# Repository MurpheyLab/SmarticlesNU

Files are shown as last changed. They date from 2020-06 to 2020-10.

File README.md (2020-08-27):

# SmarticlesNU

This repository includes all the hardware design and software files for the smarticle system. Examples can be found in Code/Python/Examples. See [Smarticle Tracking](https://github.com/murpheylab/SmarticleTracking) for the a python AprilTag tracking library and [SmarticleSimulation](https://github.com/asamland/SmarticleSimulation) for a PyBullet simulator of the system.  

All documentation for the python modules in this repository is available [here](https://murpheylab.github.io/SmarticlesNU/)

Installing Python Dependencies
------------

You can install pyserial and the XBee Python library using pip

    $ pip install pyserial
    $ pip install digi-xbee

Running Your First Program
-----------
Use the included `SmarticleSyncGait.py` to test your setup. You will have to modify `PORT_NAME` to match the USB port name of the local XBee connected to your computer.  

Run the the following command to execute the code and keep the python script open  
    
    $ python3 -i SmarticleSyncGait.py
    
Then you can run this command to run the smarticles for 1 minute  

    >>> timed_sync(1)

Interfacing with The Xbees
---
To Change the settings of the Base Xbee, use [DIGI XCTU](https://www.digi.com/resources/documentation/digidocs/90001526/tasks/t_download_and_install_xctu.htm)  
The Settings for the base Xbee are the default settings for 802.15.4 firmware with these changes:  
<br>
        **1.** Change mode (AP) to API Enabled  
        **2.** Change Pan ID (ID) to 1984  
        **3.** Ensure address (MY) is 0  
        **4.** Change Destination Low Address (DL) to 0xFFFF (broadcast)  
        
You can also modify these settings in a simple serial console by entering command mode. See this [guide](https://cdn.sparkfun.com/learn/materials/29/22AT%20Commands.pdf) for more information.
    
Modifying Code on The Smarticles
---
To modify the code on the smarticles themselves, you will also need to instal MiniCore into the Arduino IDE and an SI Labs driver for the CP2104 chip.  
  <br> 
    Get the CP210x Driver for your OS: [SI Labs Drivers Link](https://www.silabs.com/products/interface/usb-bridges/classic-usb-bridges/device.cp2104?q=cp2104;page=1;x6=searchHeader;q6=Software)  
    Download Arduino IDE: [Arduino IDE Link](https://www.arduino.cc/en/Main/Software)  
    Follow the instructions to install in Arduino IDE: [MiniCore Link](https://github.com/MCUdude/MiniCore#how-to-install) 
    <br>
    
After Installing all these dependencies you will have to move the files from the Code/Arduino folder into your local Arduino folder (usually found in documents)  
<br>
        **1.**  Move the programmable_smarticle folder into your Arduino directory (should be then documents/Arduino/programmable_smarticle)  
        **2.**  Move the contents of the repo Arduino/libraries folder into your local Arduino/libraries folder  
    
You will have to restart the Arduino IDE and then you should be able to open the programmable_smarticle.ino sketch and you should see PWMServo, NeoHWSerial, and Smarticle in the Sketch->Include Library file menu.

To upload the program to the smarticle, use the follow board configuration under the tools file menu:  

  | Field | Value|
|:------------:|:-------------------------------:| 
| Board        | ATmega328                      | 
| Clock        | 8MHz External                   |  
| BOD          | BOD 2.7V                        |  
| Compiler LTO | LTO Enabled                     |  
| Variant      | 328PB                           |  
| Bootloader   | Yes (UART0)                     |  
| Port         | select USB port of SI Labs Chip |

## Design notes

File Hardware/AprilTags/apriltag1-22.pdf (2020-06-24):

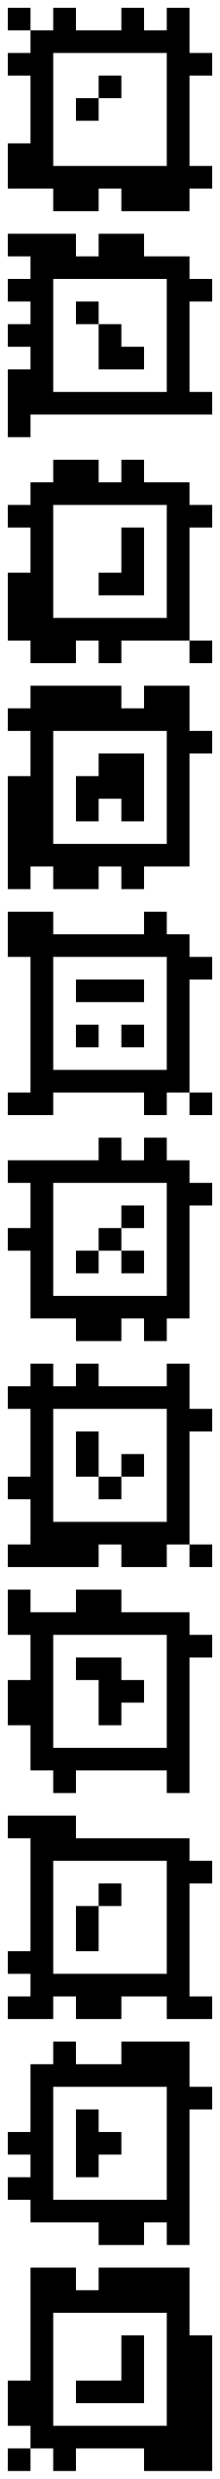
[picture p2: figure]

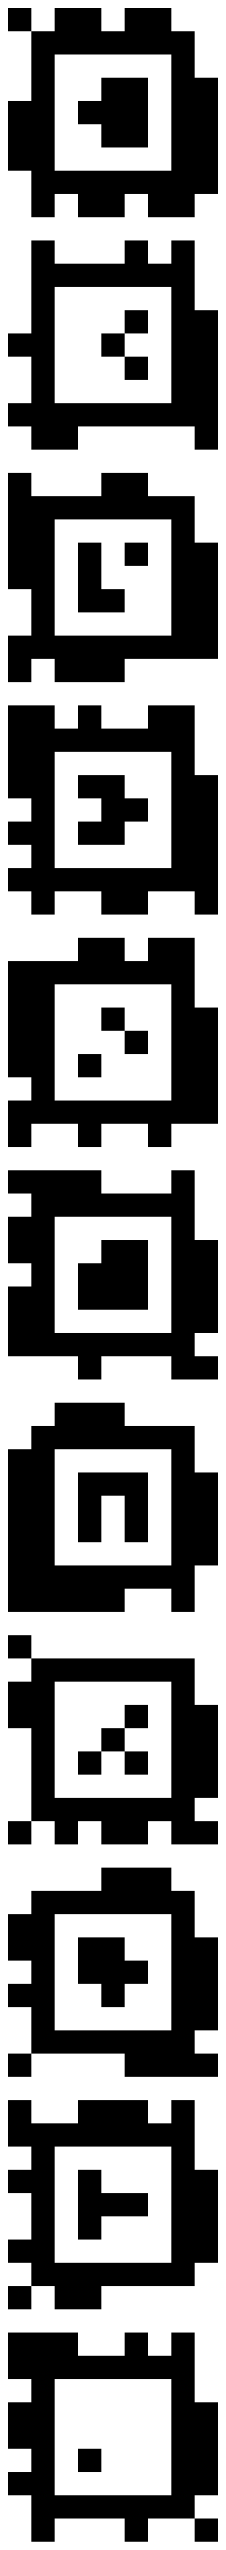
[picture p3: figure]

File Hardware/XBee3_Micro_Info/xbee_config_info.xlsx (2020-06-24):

node ID | device address (MY) | Serial No. | PAN ID | Coordinator Enable (CE) | API Mode (AP) | Destination Low Address (DL) | Serial No.
BASE | 0 | 41958C3B | 1984 | 1 | API w/esacpes (2) | FFFF (default is broadcast) | 41958C3B
smart1 | 1 | 41958CDB | 1984 | 0 | Transparent (0) | 0 | 41958CDB
smart2 | 2 | 41958C75 | 1984 | 0 | Transparent (0) | 0 | 41958C75
smart3 | 3 | 4195884A | 1984 | 0 | Transparent (0) | 0 | 4195884A
smart4 | 4 | 41958C55 | 1984 | 0 | Transparent (0) | 0 | 41958C55
smart5 | 5 | 4195890F | 1984 | 0 | Transparent (0) | 0 | 4195890F
smart6 | 6 | 41958C37 | 1984 | 0 | Transparent (0) | 0 | 41958C37
smart7 | 7 | 41958C7F | 1984 | 0 | Transparent (0) | 0 | 41958C7F
 | Serial number circled below

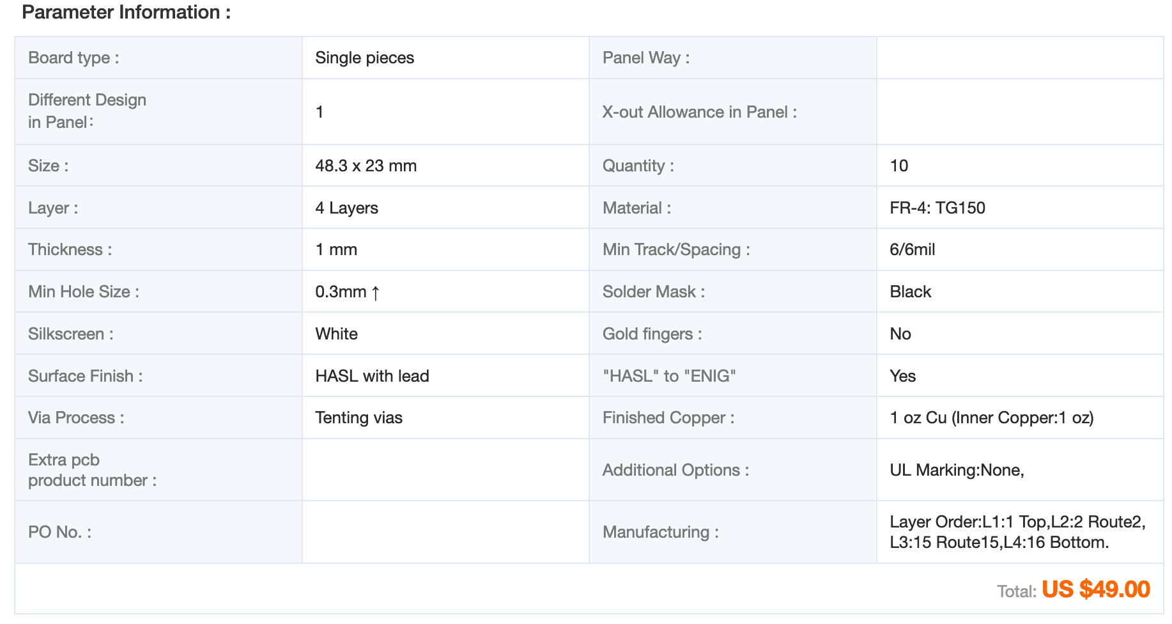
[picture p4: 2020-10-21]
Hardware/PCB/Eagle Files/PCBWay Parameters/Feather_PCBWay_params.png

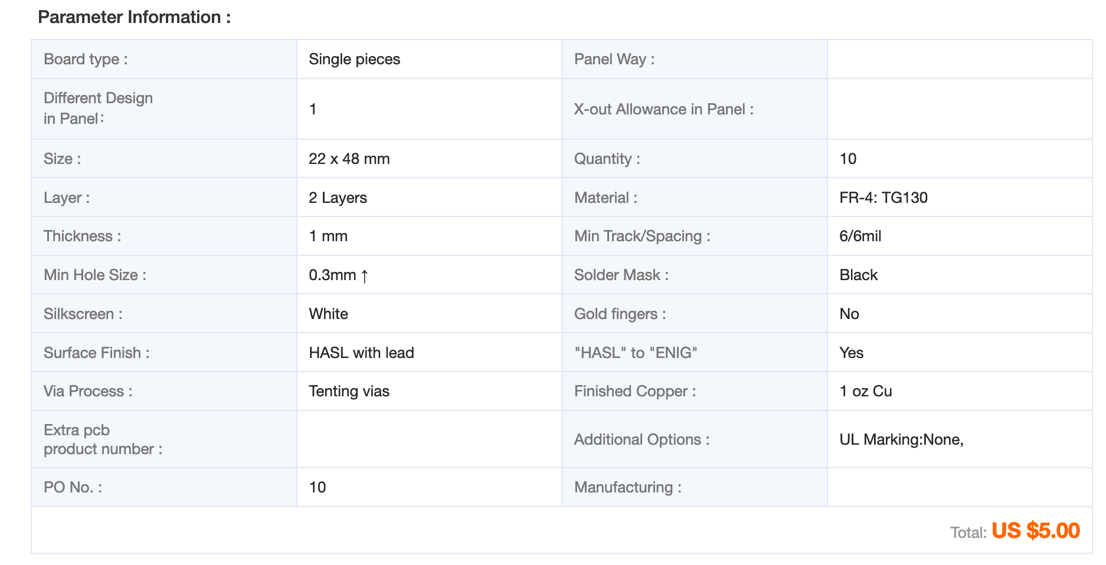
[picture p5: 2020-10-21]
Hardware/PCB/Eagle Files/PCBWay Parameters/TopBoard_PCBWay_params.png

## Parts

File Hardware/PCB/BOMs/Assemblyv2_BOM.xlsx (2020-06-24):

Item | Qty | Manufacturer | Mfg. Part No | Description
1 | 2 | Turnigy | 1440-A Servo (https://hobbyking.com/en_us/turnigytm-tgy-1440a-analog-servo-v2-0-8kg-0-10sec-4-4g.html) | Servos
2 | 1 | Molex | 51281-1294 (https://www.mouser.com/ProductDetail/Molex/51281-1294) | Connector b/w feather and top board
3 | 1 | eBoot | 1.25 mm JST 2 Pin Micro Female Connector (https://www.amazon.com/eBoot-Pairs-Electrical-Female-Connector/dp/B06WGM9W7S) | Battery connector
4 | 1 | Turnigy | nano-tech 200mAh 1S 35 (https://hobbyking.com/en_us/turnigy-nano-tech-200mah-1s-35-70c-lipoly-battery-5pcs.html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) | Battery

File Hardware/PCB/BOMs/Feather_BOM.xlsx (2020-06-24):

Item# | Ref Des | Qty | Manufacturer | Mfg Part no. | Package | Description/ Value | Type
1 | C8, C9, C11 | 3 |  |  | 0603 | 10nF | SMD
2 | C4, C6, C7, C10, C13 | 5 |  |  | 0603 | 0.1 uF | SMD
3 | C1,C14 | 2 |  |  | 0603 | 1.0uF | SMD
4 | C2,C3,C5,C12,C15 | 5 |  |  | 0603 | 10uF | SMD
5 | CON1 | 1 | Amphenol ICC | 10103594-0001LF |  | Micro B USB Connectors | SMD
6 | CON100 | 1 | Molex | 512811294 |  |  | SMD
7 | D1 | 1 |  |  | CHIP-LED 0603 | Red LED | SMD
8 | D2 | 1 | Diodes Inc. | SDM100K30L-7 | SOD-323 | Schottky Diode | SMD
9 | D3 | 1 |  |  | CHIP-LED 0603 | Orange LED | SMD
10 | Q1 | 1 | Didoes Inc. | DMG3418L | SOT23-R | P-Channel Mosfet | SMD
11 | R1, R2, R4, R6 | 4 |  |  | 0603 | 1K | SMD
12 | R3, R5, R10 | 3 |  |  | 0603 | 10k | SMD
13 | R7, R8, R9 | 3 |  |  | 0603 | 100k | SMD
14 | S1 | 1 | C&K | KMR231NG LFS |  | SMT Tact Switches | SMD
15 | S2 | 1 | C&K | PCM12SMTR |  | Single Pole, Double Throw (SPDT) Switch | SMD
16 | U1 | 1 | Microchip Technology | MCP73831T-2DCI/OT | SOT23-5 | MCP73831/2 LIPO Charger | SMD
17 | U2 | 1 | Diodes Inc. | AP2112K-3.3 | SOT23-5 | SOT23-5 Fixed Voltage Regulators | SMD
18 | U3 | 1 | Silicon Labs | CP2104 | QFN24_4MM_SMSC | CP2104 - USB to UART Bridge | SMD
19 | U4 | 1 | Microchip Technology | ATmega328PB-MUR | 32VFQFN | IC MCU 8BIT 32KB FLASH 32VFQFN | SMD
20 | U5 | 1 | Analog Devices | ADXL337BCPZ-RL | LFCSP_LQ-16 | ADXL337 Low Power 3-Axis ¬±3 g Accelerometer with Analog Output. | SMD
21 | Y1 | 1 | Murata | CSTNE8M00GH5C000R0 |  | 8mhz resonator | SMD

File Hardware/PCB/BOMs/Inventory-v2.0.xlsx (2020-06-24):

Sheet: TopBoard
Part | Value | Device | Package | Description
C1 | 9.0pF | CAP_CERAMIC_0603MP | _0603MP | Ceramic Capacitors
C2 | 1.0uF | CAP_CERAMIC_0603MP | _0603MP | Ceramic Capacitors
C3 | 0.1uF | CAP_CERAMIC_0603MP | _0603MP | Ceramic Capacitors
CON100 | 12XFFCMOLEX_51281 | 12XFFCMOLEX_51281 | MOLEX_51281-1294
PH1 | A10 | A10 | PHOTORESISTOR | Sensor Robust Light Sensing Applications
PH2 | A10 | A10 | PHOTORESISTOR | Sensor Robust Light Sensing Applications
PH3 | A10 | A10 | PHOTORESISTOR | Sensor Robust Light Sensing Applications
R1 | 10k | RESISTOR_0603MP | _0603MP | Resistors
R2 | 10k | RESISTOR_0603MP | _0603MP | Resistors
R3 | 10k | RESISTOR_0603MP | _0603MP | Resistors
R100 | 0.1 | RESISTOR_0603MP | _0603MP | Resistors
S1 |  | SWITCH-SPDT-SMD-RIGHT-ANGLE | SWITCH_SPST_SMD_A | Single Pole, Double Throw (SPDT) Switch
U1 | XBEE3 | XBEE3 | XBEE3_MICRO | XBee 3 802.15
U100 | INA180B2 | INA180B2 | SOT23-5 | 50x gain current sense amplifier

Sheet: Feather
Part | Value | Device | Package | Description
C1 | 1uF | CAP_CERAMIC_0603MP | _0603MP | Ceramic Capacitors
C2 | 10µF | CAP_CERAMIC_0603MP | _0603MP | Ceramic Capacitors
C3 | 10µF | CAP_CERAMIC_0603MP | _0603MP | Ceramic Capacitors
C4 | 0.1uF | CAP_CERAMIC_0603MP | _0603MP | Ceramic Capacitors
C5 | 10uF | CAP_CERAMIC_0603MP | _0603MP | Ceramic Capacitors
C6 | 0.1uF | CAP_CERAMIC_0603MP | _0603MP | Ceramic Capacitors
C7 | 0.1uF | CAP_CERAMIC_0603MP | _0603MP | Ceramic Capacitors
C8 | 10nF | CAP_CERAMIC_0603MP | _0603MP | Ceramic Capacitors
C9 | 10nF | CAP_CERAMIC_0603MP | _0603MP | Ceramic Capacitors
C10 | 0.1uF | CAP_CERAMIC_0603MP | _0603MP | Ceramic Capacitors
C11 | 10nF | CAP_CERAMIC_0603MP | _0603MP | Ceramic Capacitors
C12 | 10uF | CAP_CERAMIC_0603MP | _0603MP | Ceramic Capacitors
C13 | 0.1uF | CAP_CERAMIC_0603MP | _0603MP | Ceramic Capacitors
C14 | 1uF | CAP_CERAMIC_0603MP | _0603MP | Ceramic Capacitors
C15 | 10uF | CAP_CERAMIC_0603MP | _0603MP | Ceramic Capacitors
R1 | 1K | RESISTOR_0603MP | _0603MP | Resistors
R2 | 1K | RESISTOR_0603MP | _0603MP | Resistors
R3 | 10K | RESISTOR_0603MP | _0603MP | Resistors
R4 | 1K | RESISTOR_0603MP | _0603MP | Resistors
R5 | 10K | RESISTOR_0603MP | _0603MP | Resistors
R6 | 1K | RESISTOR_0603MP | _0603MP | Resistors
R7 | 100k | RESISTOR_0603MP | _0603MP | Resistors
R8 | 100k | RESISTOR_0603MP | _0603MP | Resistors
R9 | 100k | RESISTOR_0603MP | _0603MP | Resistors
R10 | 10K | RESISTOR_0603MP | _0603MP | Resistors
CON100 | 12XFFCMOLEX_51281 | 12XFFCMOLEX_51281 | MOLEX_51281-1294
D1 | RED | LED0603_NOOUTLINE | CHIPLED_0603_NOOUTLINE | LED
D2 | MBR120 | DIODE-SCHOTTKYSOD-323 | SOD-323
D3 | ORANGE | LED0603_NOOUTLINE | CHIPLED_0603_NOOUTLINE | LED
IC1 | ATMEGA328P | MEGA8-MI | MLF32-TH | MICROCONTROLLER
Q1 | DMG341 | MOSFET-P | SOT23-R | P-Channel Mosfet
S1 |  | SWITCH-SPDT-SMD-RIGHT-ANGLE | SWITCH_SPST_SMD_A | Single Pole, Double Throw (SPDT) Switch
SW1 | KMR2 | SWITCH_TACT_SMT4.6X2.8 | BTN_KMR2_4.6X2.8 | SMT Tact Switches
U$1 | ADXL337 | ADXL337 | LFCSP_LQ-16 | ADXL337 Low Power 3-Axis ¬±3 g Accelerometer with Analog Output.
U1 | MCP73831T-2ACI/OT | MCP73831/2 | SOT23-5 | MCP73831/2 LIPO Charger
U2 | AP2112-3.3 | VREG_SOT23-5 | SOT23-5 | SOT23-5 Fixed Voltage Regulators
U3 | CP2104 | CP2104 | QFN24_4MM_SMSC | CP2104 - USB to UART Bridge
X1 | 20329 | USB_MICRO_20329_V2 | 4UCONN_20329_V2 | USB Connectors
Y1 | RESONATORMU | RESONATORMU | RESONATOR

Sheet: Summary
Component | qty | package | manufacturer | part number | board | notes
Capacitors | 18
10nF Cap | 3 | _0603 |  |  | Feather | accelerometer
0.1 uF Cap | 5 | _0603 |  |  | Feather
1.0uF Cap | 2 | _0603 |  |  | Feather
10uF Cap | 5 | _0603 |  |  | Feather
0.1 uF Cap | 1 | _0603 |  |  | Top
9pF Cap | 1 | _0603 |  |  | Top
1.0 uF Cap | 1 | _0603 |  |  | Top
Resistors | 14
1K Res | 4 | _0603 |  |  | Feather
10K Res | 3 | _0603 |  |  | Feather
100k Res | 3 | _0603 |  |  | Feather
10K Res | 3 | _0603 |  |  | Top
0.1 Res | 1 | _0603 |  |  | Top | current sense
Resonator | 1
8mhz resonator | 1 | SMD_wide | Murata | CSTNE8M00GH5C000R0 | Feather
Diodes | 3
Orange LED | 1 | _0603 |  |  | Feather
Red LED | 1 | _0603 |  |  | Feather
Schotky Diode | 1 | SOD-323 | Diodes, Inc. | SDM100K30L-7 | Feather
ICs | 6
ATMEGA 328PB | 1 | 32VQFN | Microchip Technology | ATmega328PB-MUR | Feather
Lipo Charger | 1 | SOT23-5 | Microchip Technology | MCP73831T-2DCI/OT | Feather
500mA 3.3V regulator | 1 | SOT23-5 | Diodes Inc. | AP2112K-3.3 | Feather
3-axis accelerometer | 1 | LFCSP_LQ-16 | Analog Devices | ADXL337BCPZ-RL | Feather
Serial Chip | 1 | QFN24_4MM_SMSC | Silicon Labs | CP2104 | Feather
Xbee3 Micro | 1 | Micro | Digi International | XB3-24ACM-J | Top
Current Sense Amp | 1 | SOT23-5 | Texas Instruments | INA180B2 | Top
Transistors | 1
P-channel Mosfet | 1 | SOT23-5 | Didoes Inc. | DMG3418L | Feather
Switches | 2
Slide Switch | 1 | - | C&K | PCM12SMTR | Feather
Slide Switch | 1 | - | C&K | PCM12SMTR | Top
Button Switch | 1 | BTN_KMR2_4.6X2.8 | C&K | KMR231NG LFS | Feather
Connectors | 4
Micro USB port | 1 | 4UCONN_20329_V2 | unknown | 98-MB05PMXX-01 | Feather
12pin FFC | 1 | - | Molex | Molex 15166-0117 | Feather/Top
12pin FFC connector | 2 |  | Molex | 512811294 | Feather and Top
External Components
PhotoResistor | 3 | PTH |  | PDV-P9007-ND | Top
Servo | 2 |  |  | TGY-1440A | N/A
Li-Po 1S | 1 |  |  | Turnigy 150mAh 0.15C

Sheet: Current Inventory
Component | package | Digi-Key Part number (or vendor) | part number | updated qty | Purchased | Manual Adjustments | Feathers Made | TopBoards Made | Assemblies Made | qty as of 1/23/20
 |  |  |  |  |  |  | 0 | 0 | 0
Capacitors
9pF Cap | _0603 |  |  | 87 | 0 | 0 | 0 | 1 | 0 | 87
10nF Cap | _0603 |  |  | 88 | 0 | 0 | 3 | 0 | 0 | 88
0.1 uF Cap | _0603 |  |  | 917 | 0 | 0 | 5 | 1 | 0 | 917
1.0uF Cap | _0603 |  |  | 449 | 0 | 0 | 2 | 1 | 0 | 449
10uF Cap | _0603 |  |  | 430 | 0 | 0 | 5 | 0 | 0 | 430
Resistors
0.1 Res | _0603 |  |  | 104 | 0 | 0 |  | 1 | 0 | 104
1K Res | _0603 |  |  | 924 | 0 | 0 | 4 | 0 | 0 | 924
10K Res | _0603 |  |  | 909 | 0 | 0 | 3 | 3 | 0 | 909
100k Res | _0603 |  |  | 948 | 0 | 0 | 3 | 0 | 0 | 948
Resonator
8mhz resonator | SMD_wide |  | CSTNE8M00GH5C000R0 | 2 | 0 | 0 | 1 | 0 | 0 | 2
Diodes
Orange LED | _0603 |  |  | 0 | 0 | 0 | 1 | 0 | 0 | 0
Yellow LED | _0603 |  |  | 25 | 0 | 0 | 0 | 0 | 0 | 25
Red LED | _0603 |  |  | 0 | 0 | 0 | 1 | 0 | 0 | 0
Schotky Diode | SOD-323 |  | SDM100K30L-7‎ | 2 | 0 | 0 | 1 | 0 | 0 | 2
ICs
ATMEGA 328PB | MLF-32TH |  |  | 1 | 0 | 0 | 1 | 0 | 0 | 1
Lipo Charger | SOT23-5 |  | MCP73831T-2ACI/OT | 1 | 0 | 0 | 1 | 0 | 0 | 1
500mA 3.3V regulator | SOT23-5 |  | AP2112-3.3 | 1 | 0 | 0 | 1 | 0 | 0 | 1
3-axis accelerometer | LFCSP_LQ-16 |  | ADXL337 | 3 | 0 | 0 | 0 | 0 | 0 | 3
Serial Chip | QFN24_4MM_SMSC |  | CP2102N | 6 | 0 | 0 | 1 | 0 | 0 | 6
Xbee3 Micro | Micro |  | XB3-24ACM-J | 6 | 0 | 0 | 0 | 1 | 0 | 6
Current Sense Amp | SOT23-5 |  | INA180B2 | 8 | 0 | 0 | 0 | 1 | 0 | 8
Transistors
P-channel Mosfet | SOT23-5 |  | DMG341 | 5 | 0 | 0 | 1 | 0 | 0 | 5
Switches
Slide Switch | - |  | Sparkfun COM-10860 | 7 | 0 | 0 | 1 | 1 | 0 | 7
Button Switch | BTN_KMR2_4.6X2.8 |  | BTN_KMR2_4.6X2.8 | 10 | 0 | 0 | 1 | 0 | 0 | 10
Connectors
Micro USB port | 4UCONN_20329_V2 |  | Adafruit micro USB | 7 | 0 | 0 | 1 | 0 | 0 | 7
12pin FFC | - |  | Molex 15166-0117 | 9 | 0 | 0 | 0 | 1 | 0 | 9
12pin FFC connector |  |  | MOLEX_51281-1294 | 6 | 0 | 0 | 1 | 1 | 0 | 6
Battery Connector |  |  |  | 1 | 0 | 0 | 0 | 0 | 1 | 1
External Components
PhotoResistor | PTH |  |  | 6 | 0 | 0 | 0 | 3 | 0 | 6
Servo |  | HobbyKing | TGY-1440A | 9 | 0 | 4 | 0 | 0 | 2 | 13
Li-Po 1S |  | HobbyKing | Turnigy 150mAh 0.15C | 6 | 0 | 2 | 0 | 0 | 1 | 8
PCBs
Feather-board |  |  |  | 3 | 0 | 0 | 1 | 0 | 0 | 3
top board |  |  |  | 3 | 0 | 0 | 0 | 1 | 0 | 3
Old Parts
300 Ohm Resistor | _0603 |  |  | 100
4.7 uF Cap | _0603 |  |  | 90
100pF Cap | _0603 |  |  | 90
Mems Mic |  |  | ADMP401 | 10
Op Amp | SOT23-5 |  | OPA344 | 10
Last updated: | 2020-01-23

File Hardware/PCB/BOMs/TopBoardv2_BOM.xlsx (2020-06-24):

Item | Ref Des | Qty | Manufacturer | Mfg. Part No | Package | Description/Value | Type
1 | C1 | 1 |  |  | 0603 | 9.0pF | SMD
2 | C2 | 1 |  |  | 0603 | 1.0uF | SMD
3 | C3 | 1 |  |  | 0603 | 0.1uF | SMD
4 | CON100 | 1 | Molex | 51281-1294 |  |  | SMD
5 | PH1, PH2, PH3 | 3 | Advanced Photonics | PDV-P9007 |  |  | PTH
6 | R1, R2, R3 | 3 |  |  | 0603 | 10k | SMD
7 | R100 | 1 |  |  | 0603 | 0.1 | SMD
8 | S1 | 1 | C&K | PCM12SMTR |  | Single Pole, Double Throw (SPDT) Switch | SMD
9 | U1 | 1 | Digi | XB3-24ACM-J |  |  | SMD
10 | U100 | 1 | Texas Instruments | INA180B2 | SOT23-5 | Current Sense Op-Amp | SMD

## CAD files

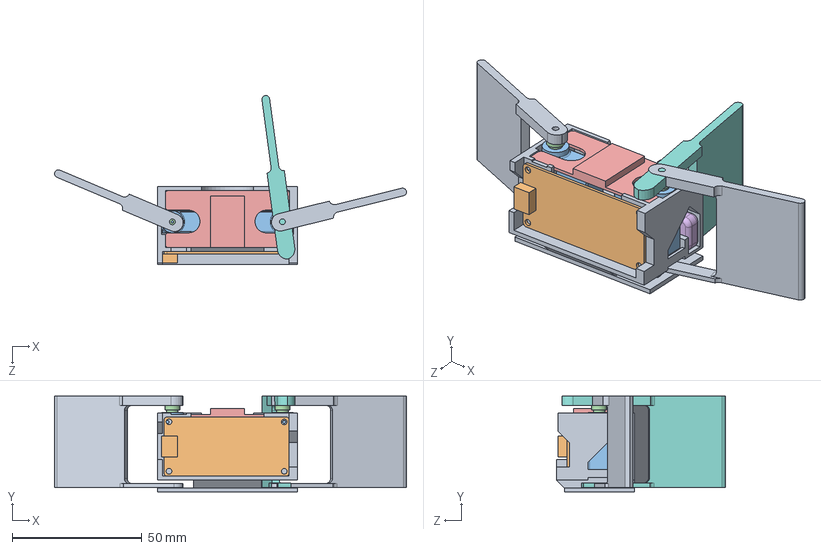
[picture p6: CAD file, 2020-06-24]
Hardware/Solidworks/NU-SmarticleDesign/Smarticle_Assembly.SLDASM
135.8 x 36.9 x 65.2 mm
Feather
Servo - Body x 2
Servo - Horn x 2
Battery - Body
Battery - Connector
TopBoard
Arm2 x 2

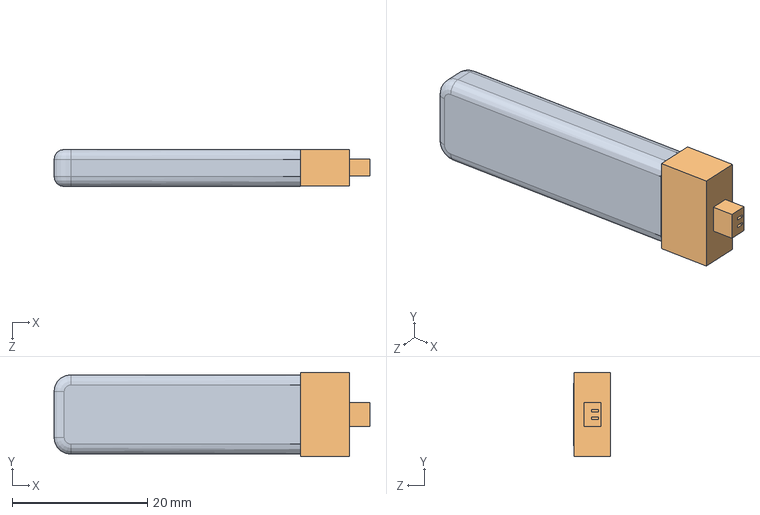
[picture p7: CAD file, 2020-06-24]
Hardware/Solidworks/NU-SmarticleDesign/battery/Battery - Assembly.SLDASM
46.8 x 12.5 x 5.50 mm
Battery - Body
Battery - Connector

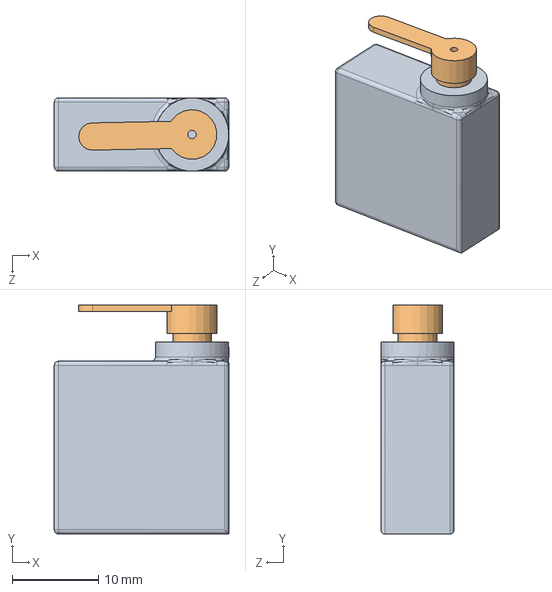
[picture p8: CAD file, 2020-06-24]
Hardware/Solidworks/NU-SmarticleDesign/servo/Servo - Assembly.SLDASM
20.2 x 26.5 x 8.50 mm
Servo - Body
Servo - Horn

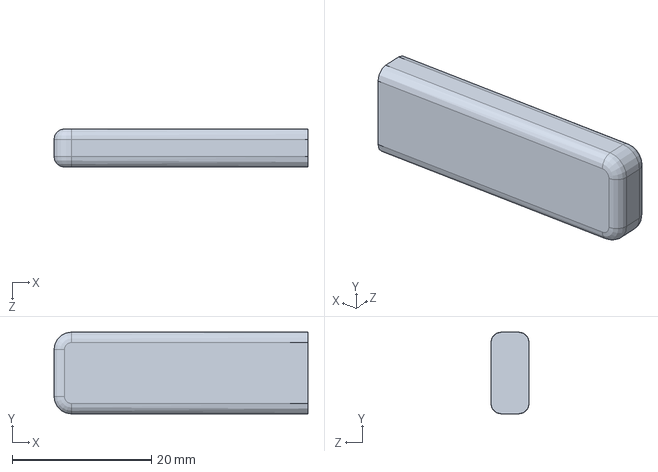
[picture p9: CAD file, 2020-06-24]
Hardware/Solidworks/NU-SmarticleDesign/battery/Battery - Body.SLDPRT
36.5 x 11.8 x 5.50 mm

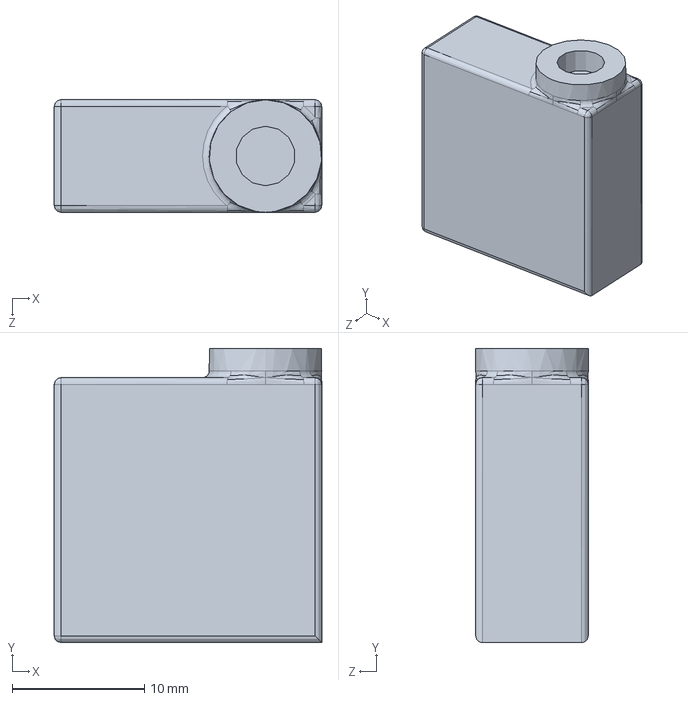
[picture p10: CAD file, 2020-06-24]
Hardware/Solidworks/NU-SmarticleDesign/servo/Servo - Body.SLDPRT
20.2 x 22.2 x 8.50 mm

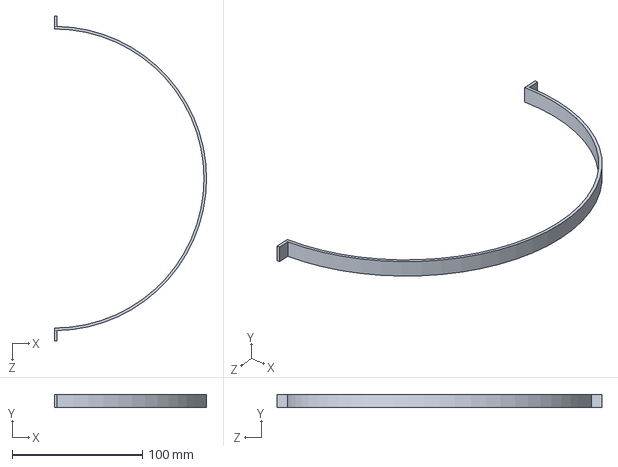
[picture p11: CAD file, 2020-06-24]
Hardware/Solidworks/SmarticleRings/230mm_ring.SLDPRT
117.0 x 10.0 x 250.0 mm

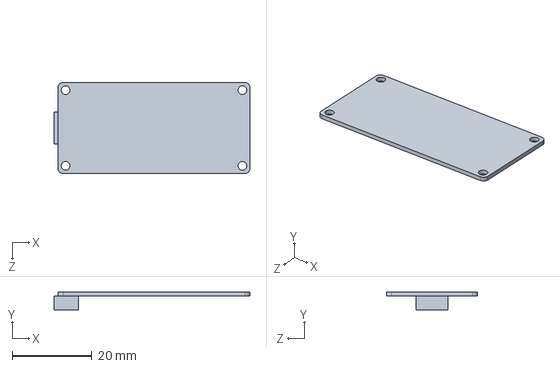
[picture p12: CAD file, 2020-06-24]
Hardware/Solidworks/NU-SmarticleDesign/Feather.SLDPRT
49.3 x 4.50 x 22.9 mm

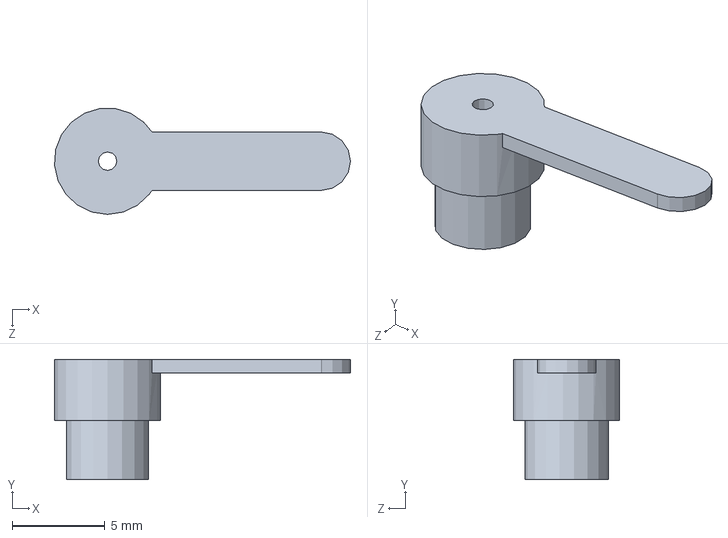
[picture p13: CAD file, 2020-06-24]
Hardware/Solidworks/NU-SmarticleDesign/servo/Servo - Horn.SLDPRT
16.0 x 6.50 x 5.72 mm

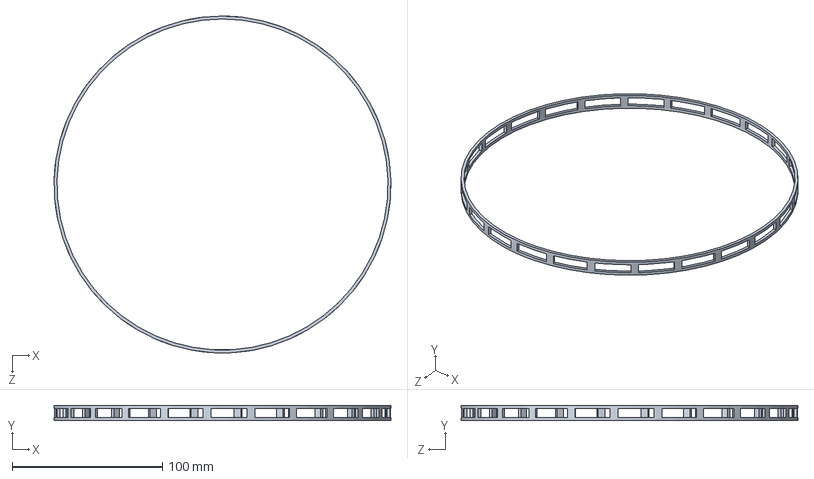
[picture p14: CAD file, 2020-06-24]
Hardware/Solidworks/SmarticleRings/220mm_ring.SLDPRT
223.9 x 10.0 x 224.0 mm

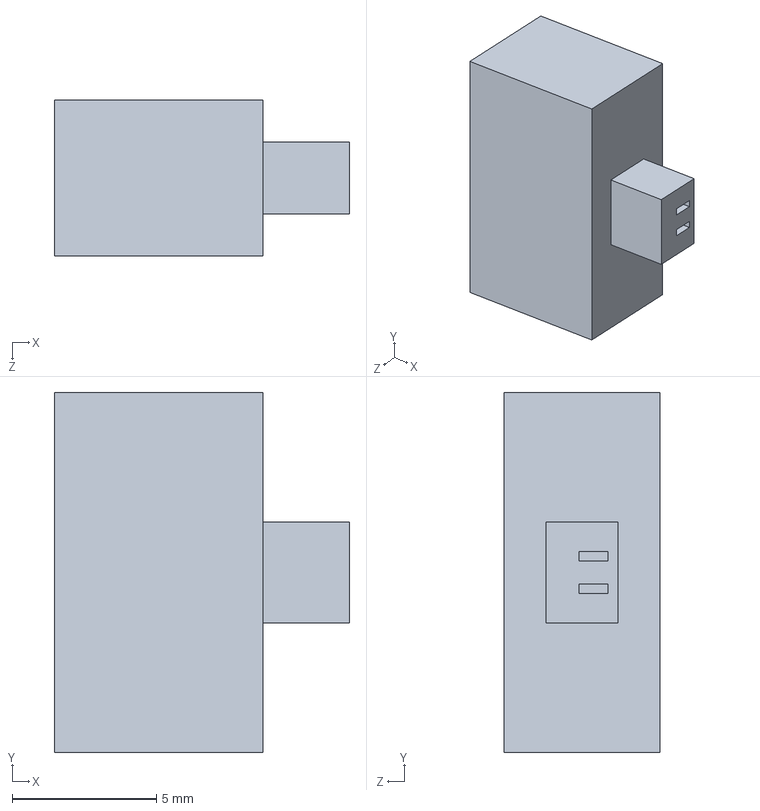
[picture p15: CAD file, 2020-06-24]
Hardware/Solidworks/NU-SmarticleDesign/battery/Battery - Connector.SLDPRT
10.2 x 12.5 x 5.40 mm

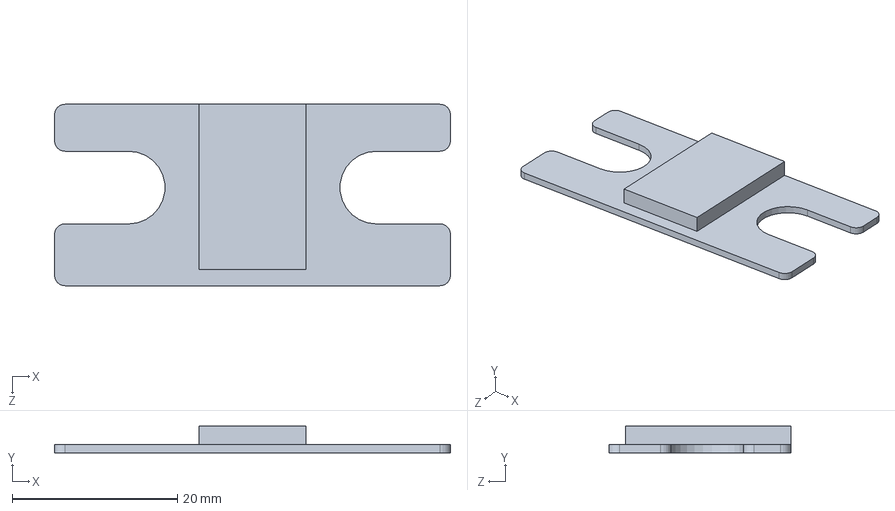
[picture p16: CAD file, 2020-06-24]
Hardware/Solidworks/NU-SmarticleDesign/TopBoard.SLDPRT
48.0 x 3.25 x 22.0 mm

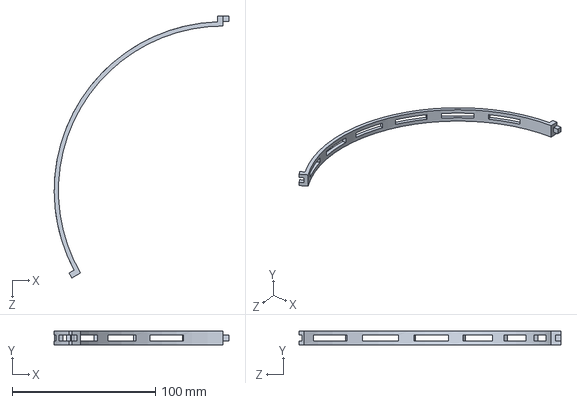
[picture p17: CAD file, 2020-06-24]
Hardware/Solidworks/SmarticleRings/230mm_ring_thirds.SLDPRT
122.0 x 10.0 x 183.0 mm

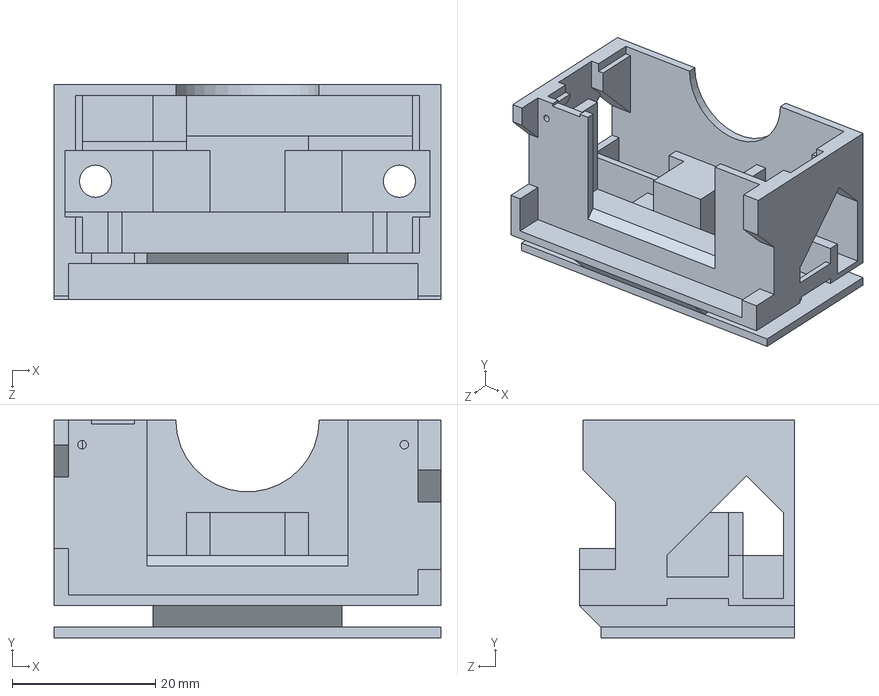
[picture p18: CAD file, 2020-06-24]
Hardware/Solidworks/NU-SmarticleDesign/Body.SLDPRT
54.0 x 30.4 x 30.0 mm

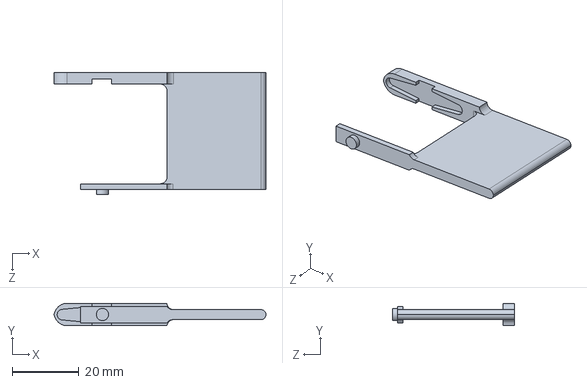
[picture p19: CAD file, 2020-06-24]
Hardware/Solidworks/NU-SmarticleDesign/servo/Servo - Solar Arm.SLDPRT
63.7 x 6.75 x 36.7 mm

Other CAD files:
Hardware/Solidworks/SmarticleRings/192mm_ring.SLDPRT
Hardware/Solidworks/NU-SmarticleDesign/Arm.SLDPRT
Hardware/Solidworks/SmarticleRings/211mm_ring_thirds.SLDPRT
Hardware/Solidworks/SmarticleRings/200mm_ring_thirds.SLDPRT
Hardware/Solidworks/SmarticleRings/192mm_ring.STL
Hardware/Solidworks/SmarticleRings/200mm_ring_thirds.STL
Hardware/Solidworks/SmarticleRings/211mm_ring_thirds.STL
Hardware/Solidworks/SmarticleRings/220mm_ring.STL
Hardware/Solidworks/SmarticleRings/230mm_ring.STL
Hardware/Solidworks/SmarticleRings/230mm_ring_thirds.STL

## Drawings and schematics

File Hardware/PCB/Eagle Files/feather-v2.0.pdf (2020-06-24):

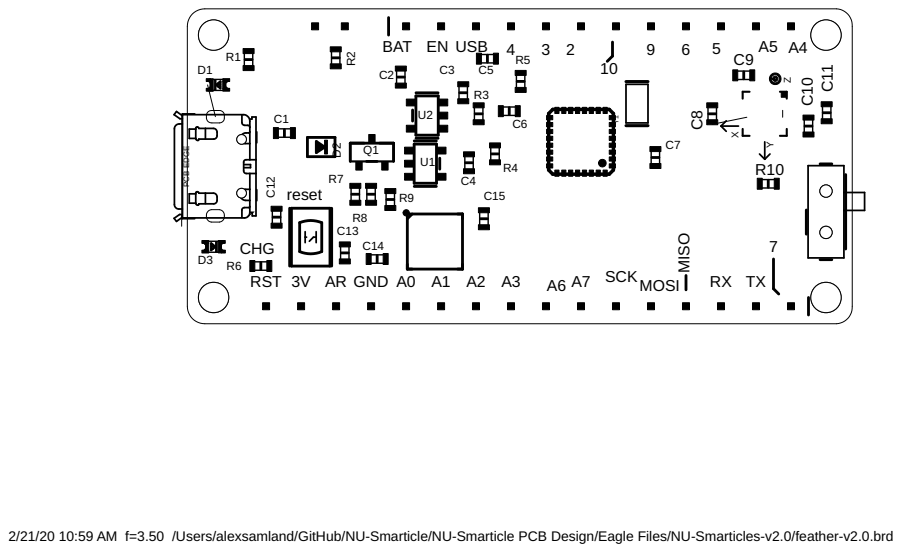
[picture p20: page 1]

2/21/20 10:59 AM f=3.50 /Users/alexsamland/GitHub/NU-Smarticle/NU-Smarticle PCB Design/Eagle Files/NU-Smarticles-v2.0/feather-v2.0.brd

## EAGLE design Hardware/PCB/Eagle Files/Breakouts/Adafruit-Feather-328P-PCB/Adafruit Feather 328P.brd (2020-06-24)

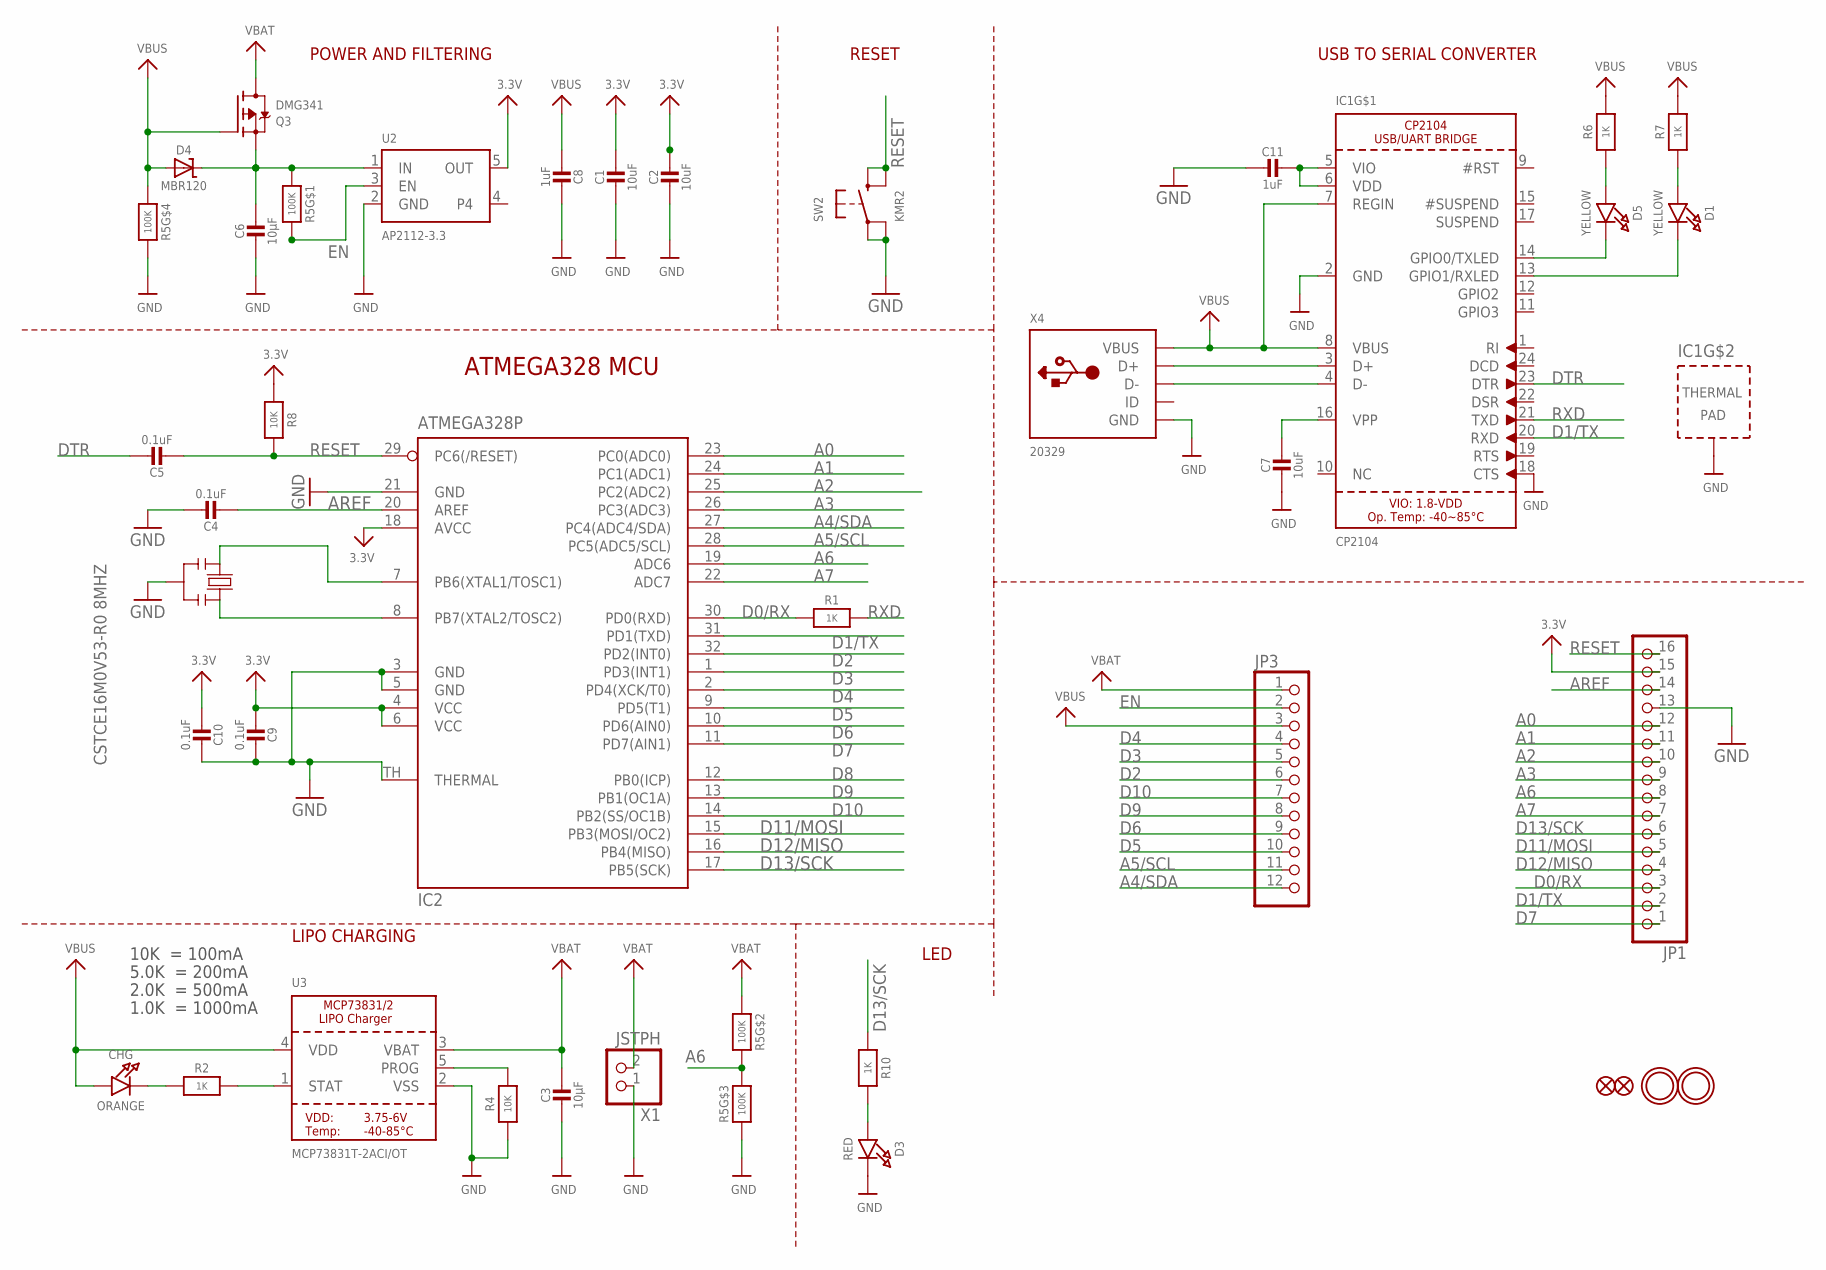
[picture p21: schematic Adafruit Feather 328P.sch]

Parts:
C1, C2: 10uF; 0805-NO
C3, C6: 10µF; 0805-NO
C4, C5, C9, C10: 0.1uF; 0603-NO
C7: 10uF; _0805MP
C8, C11: 1uF; 0603-NO
CHG: ORANGE; CHIPLED_0805_NOOUTLINE
D1, D5: YELLOW; CHIPLED_0805_NOOUTLINE
D3: RED; CHIPLED_0805_NOOUTLINE
D4: MBR120; SOD-123
IC1: CP2104; QFN24_4MM_SMSC
IC2: ATMEGA328P; MLF32-TH
JP1: HEADER-1X16ROUND; 1X16_ROUND
JP3: HEADER-1X12; 1X12_ROUND
Q3: DMG341; SOT23-R
R1: 1K; _0603MP
R2, R6, R7, R10: 1K; 0603-NO
R4, R8: 10K; 0603-NO
R5: 100K; RESPACK_4X0603
SW2: KMR2; BTN_KMR2_4.6X2.8
U2: AP2112-3.3; SOT23-5
U3: MCP73831T-2ACI/OT; SOT23-5
U$31, U$32: MOUNTINGHOLE2.5; MOUNTINGHOLE_2.5_PLATED
U$34, U$35: FIDUCIAL_1MM
X1: JSTPH; JSTPH2
X4: 20329; 4UCONN_20329_V2
Y2: CSTCE16M0V53-R0 8MHZ; RESONATOR

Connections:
3.3V: C1.1, C2.1, C9.2, C10.2, IC2.4 (VCC), IC2.6 (VCC), IC2.18 (AVCC), JP1.15, R8.2, U2.5 (OUT)
A0: IC2.23 (PC0(ADC0)), JP1.12
A1: IC2.24 (PC1(ADC1)), JP1.11
A2: IC2.25 (PC2(ADC2)), JP1.10
A3: IC2.26 (PC3(ADC3)), JP1.9
A4/SDA: IC2.27 (PC4(ADC4/SDA)), JP3.12
A5/SCL: IC2.28 (PC5(ADC5/SCL)), JP3.11
A6: IC2.19 (ADC6), JP1.8, R5.6 (2), R5.7 (2)
A7: IC2.22 (ADC7), JP1.7
AREF: C4.2, IC2.20 (AREF), JP1.14
D0/RX: IC2.30 (PD0(RXD)), JP1.3, R1.1
D1/TX: IC1.20 (RXD), IC2.31 (PD1(TXD)), JP1.2
D2: IC2.32 (PD2(INT0)), JP3.6
D3: IC2.1 (PD3(INT1)), JP3.5
D4: IC2.2 (PD4(XCK/T0)), JP3.4
D5: IC2.9 (PD5(T1)), JP3.10
D6: IC2.10 (PD6(AIN0)), JP3.9
D7: IC2.11 (PD7(AIN1)), JP1.1
D8: IC2.12 (PB0(ICP))
D9: IC2.13 (PB1(OC1A)), JP3.8
D10: IC2.14 (PB2(SS/OC1B)), JP3.7
D11/MOSI: IC2.15 (PB3(MOSI/OC2)), JP1.5
D12/MISO: IC2.16 (PB4(MISO)), JP1.4
D13/SCK: IC2.17 (PB5(SCK)), JP1.6, R10.1
DTR: C5.1, IC1.23 (DTR)
EN: JP3.2, R5.8 (2), U2.3 (EN)
GND: C1.2, C2.2, C3.2, C4.1, C6.2, C7.2, C8.1, C9.1, C10.1, C11.2, D3.C, IC1.2 (GND), IC1.18 (CTS), IC1.THERM (TP), IC2.3 (GND), IC2.5 (GND), IC2.21 (GND), IC2.TH (THERMAL), JP1.13, R4.1, R5.3 (1), R5.5 (2), SW2.A, SW2.A' (P1), U2.2 (GND), U3.2 (VSS), X1.1, X4.BASE@1 (GND), X4.BASE@2 (GND), X4.GND, X4.SPRT@1 (GND), X4.SPRT@2 (GND), X4.SPRT@3 (GND), X4.SPRT@4 (GND), Y2.2
unnamed: CHG.C, R2.1
unnamed: IC1.3 (D+), X4.D+
unnamed: R2.2, U3.1 (STAT)
unnamed: R4.2, U3.5 (PROG)
unnamed: D3.A, R10.2
unnamed: IC1.4 (D-), X4.D-
unnamed: C6.1, D4.C, Q3.2 (S), R5.1, U2.1 (IN)
unnamed: D1.A, R7.1
unnamed: D5.A, R6.1
unnamed: C11.1, IC1.5 (VIO), IC1.6 (VDD)
unnamed: C7.1, IC1.16 (VPP)
RESET: C5.2, IC2.29 (PC6(/RESET)), JP1.16, R8.1, SW2.B (S), SW2.B' (S1)
RXD: IC1.21 (TXD), R1.2
RXLED: D1.C, IC1.13 (GPIO1/RXLED)
TXLED: D5.C, IC1.14 (GPIO0/TXLED)
VBAT: C3.1, JP3.1, Q3.3 (D), R5.2 (1), U3.3 (VBAT), X1.2
VBUS: C8.2, CHG.A, D4.A, IC1.7 (REGIN), IC1.8 (VBUS), JP3.3, Q3.1 (G), R5.4 (1), R6.2, R7.2, U3.4 (VDD), X4.VBUS
XTAL1: IC2.8 (PB7(XTAL2/TOSC2)), Y2.3
XTAL2: IC2.7 (PB6(XTAL1/TOSC1)), Y2.1

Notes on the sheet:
POWER AND FILTERING
RESET
10K = 100mA
5.0K = 200mA
2.0K = 500mA
1.0K = 1000mA
USB TO SERIAL CONVERTER
LIPO CHARGING
LED
ATMEGA328 MCU

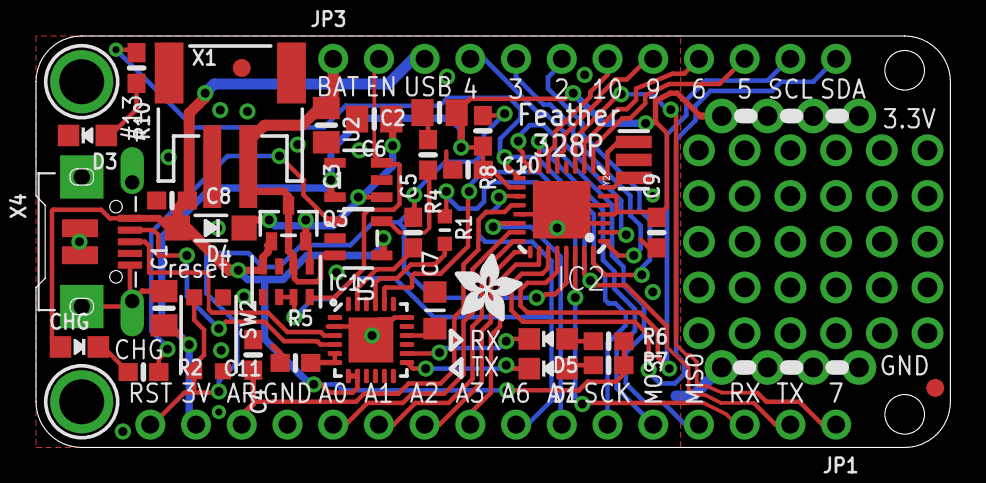
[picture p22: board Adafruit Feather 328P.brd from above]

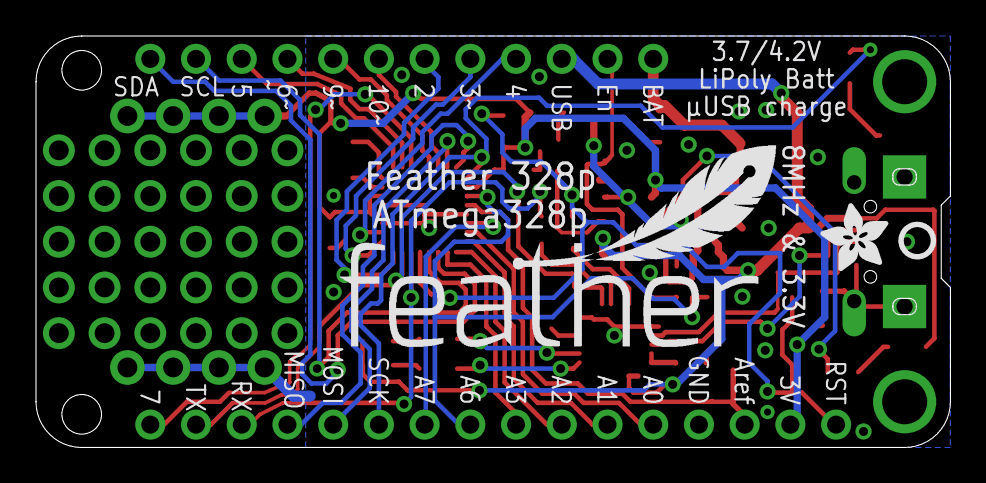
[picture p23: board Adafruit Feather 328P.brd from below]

Board: 2 copper layers, 50.8 x 22.9 mm, 43 parts (3 on the bottom side), 45 nets.

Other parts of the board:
U$9: FEATHERLOGO
U$13: PCBFEAT-REV-040
U$15, U$44: ADAFRUIT_3.5MM

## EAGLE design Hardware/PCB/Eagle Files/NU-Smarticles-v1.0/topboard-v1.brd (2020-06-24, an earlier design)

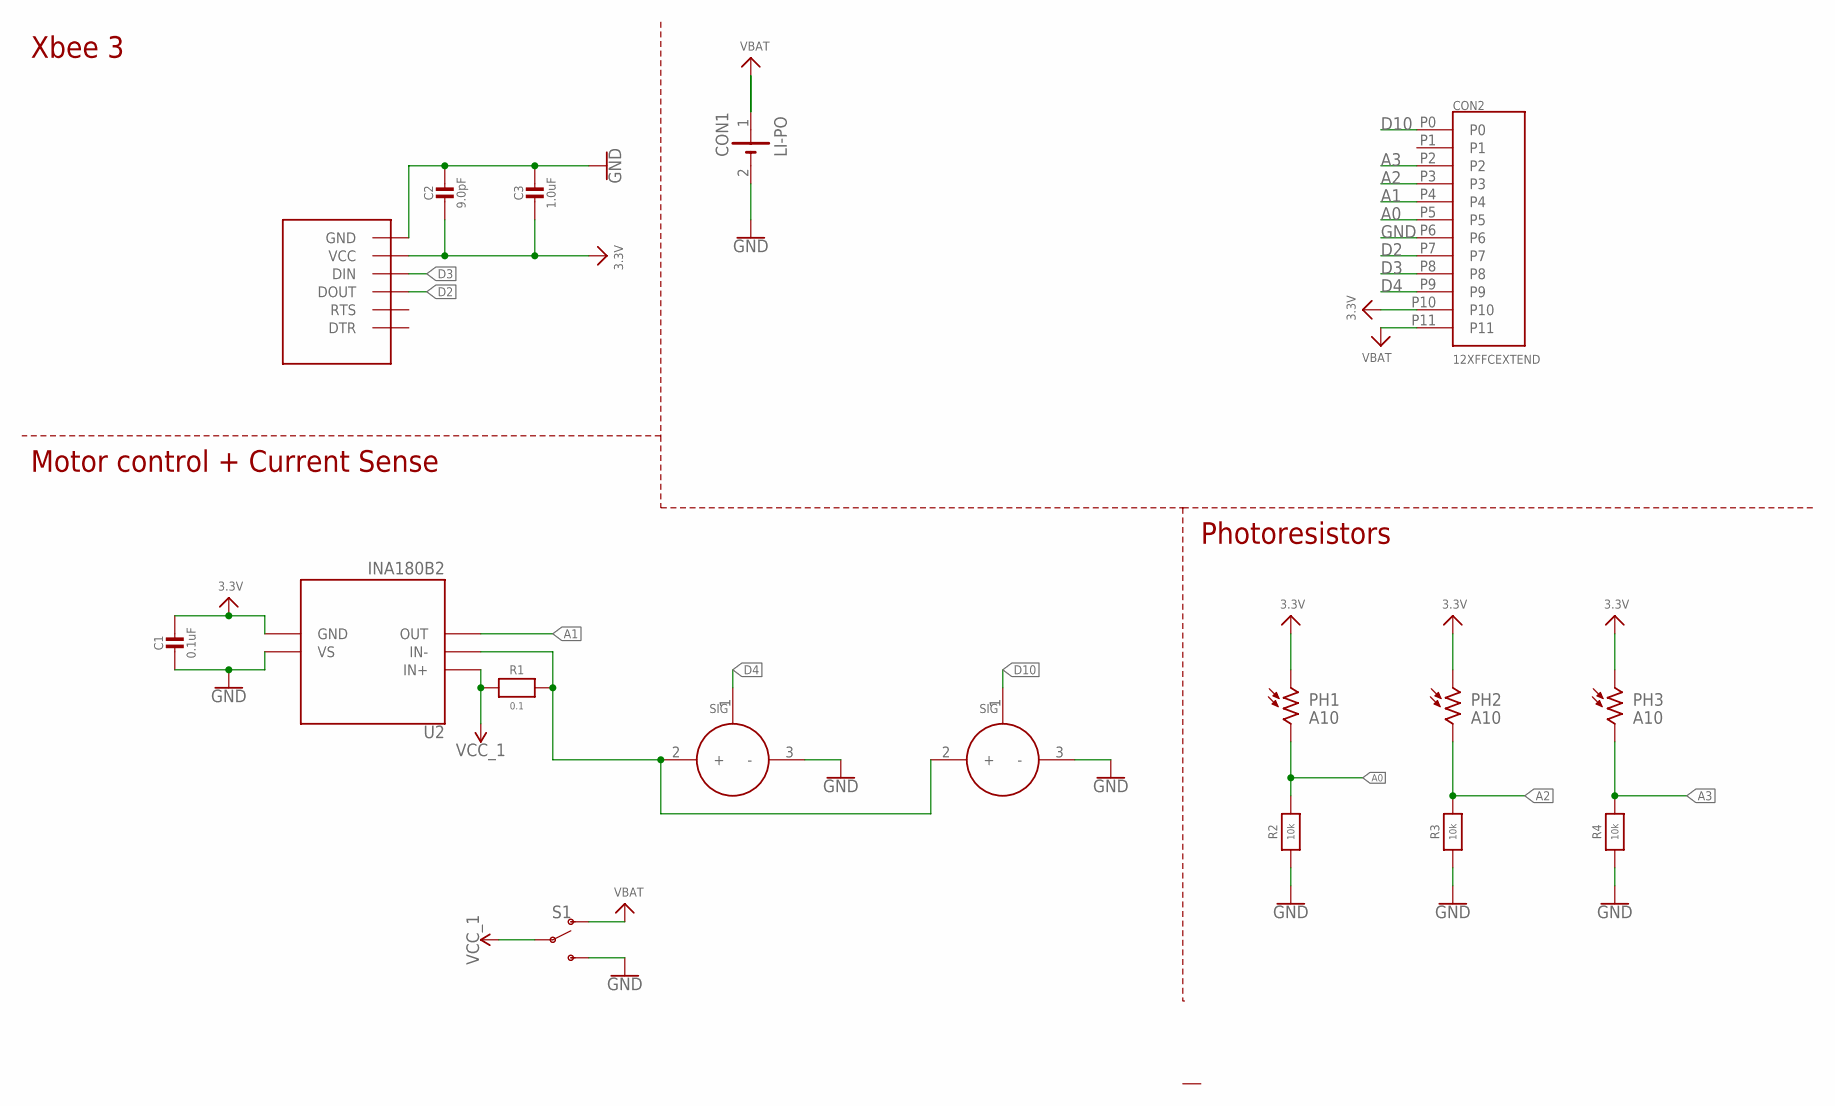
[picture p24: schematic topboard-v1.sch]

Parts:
C1: 0.1uF; _0603MP
C2: 9.0pF; _0603MP
C3: 1.0uF; _0603MP
CON1: LI-PO; 1X02_BATT
CON2: 12XFFCEXTEND; 15166-0117_XTEND
M1, M2: SERVO; 1X03_SERVO
PH1, PH2, PH3: A10; PHOTORESISTOR
R1: 0.1; _0603MP
R2, R3, R4: 10k; _0603MP
S1: SWITCH-SPDT-SMD-RIGHT-ANGLE; SWITCH_SPST_SMD_A
U1: XBEE3; XBEE3_MICRO
U2: INA180B2; SOT23-5

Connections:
3.3V: C1.1, C2.2, C3.2, CON2.P10, PH1.1, PH2.1, PH3.1, U1.VCC, U2.2 (GND)
A0: CON2.P5, PH1.2, R2.2
A1: CON2.P4, U2.4 (OUT)
A2: CON2.P3, PH2.2, R3.2
A3: CON2.P2, PH3.2, R4.2
D2: CON2.P7, U1.DOUT/DIO13 (DOUT)
D3: CON2.P8, U1.DIN/CONFIG/DIO14 (DIN)
D4: CON2.P9, M1.1 (SIG)
D10: CON2.P0, M2.1 (SIG)
GND: C1.2, C2.1, C3.1, CON1.2 (-), CON2.P6, M1.3 (-), M2.3 (-), R2.1, R3.1, R4.1, S1.3 (S), U1.GND1 (GND), U1.GND2 (GND), U1.GND3 (GND), U1.GND4 (GND), U1.GND5 (GND), U1.GND6 (GND), U2.5 (VS)
unnamed: M1.2 (+), M2.2 (+), R1.2, U2.3 (IN-)
VBAT: CON1.1 (+), CON2.P11, S1.1 (O)
VCC_1: R1.1, S1.2, U2.1 (IN+)

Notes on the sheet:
Xbee 3
Photoresistors
Motor control + Current Sense

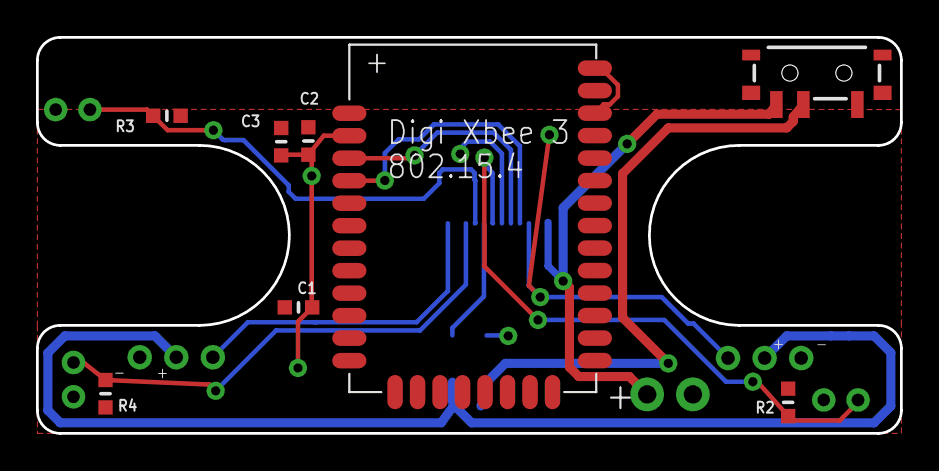
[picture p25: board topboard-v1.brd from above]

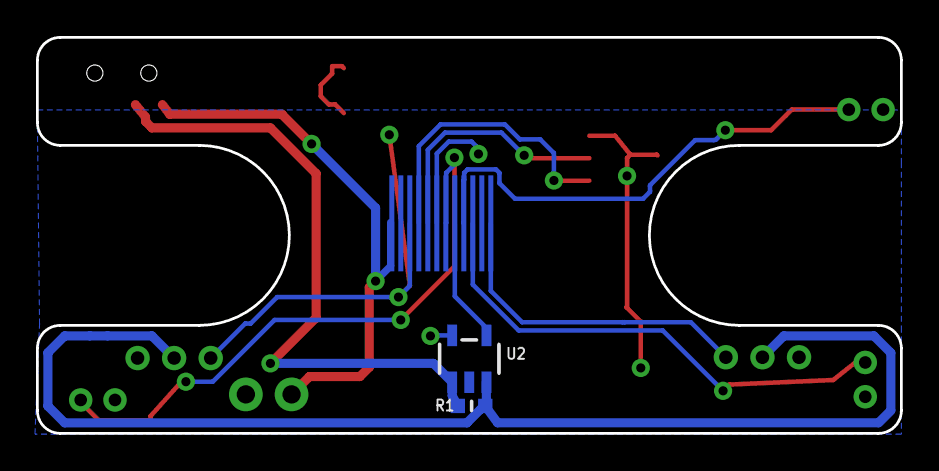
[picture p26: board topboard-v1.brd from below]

Board: 2 copper layers, 48.0 x 22.0 mm, 17 parts (3 on the bottom side), 13 nets.

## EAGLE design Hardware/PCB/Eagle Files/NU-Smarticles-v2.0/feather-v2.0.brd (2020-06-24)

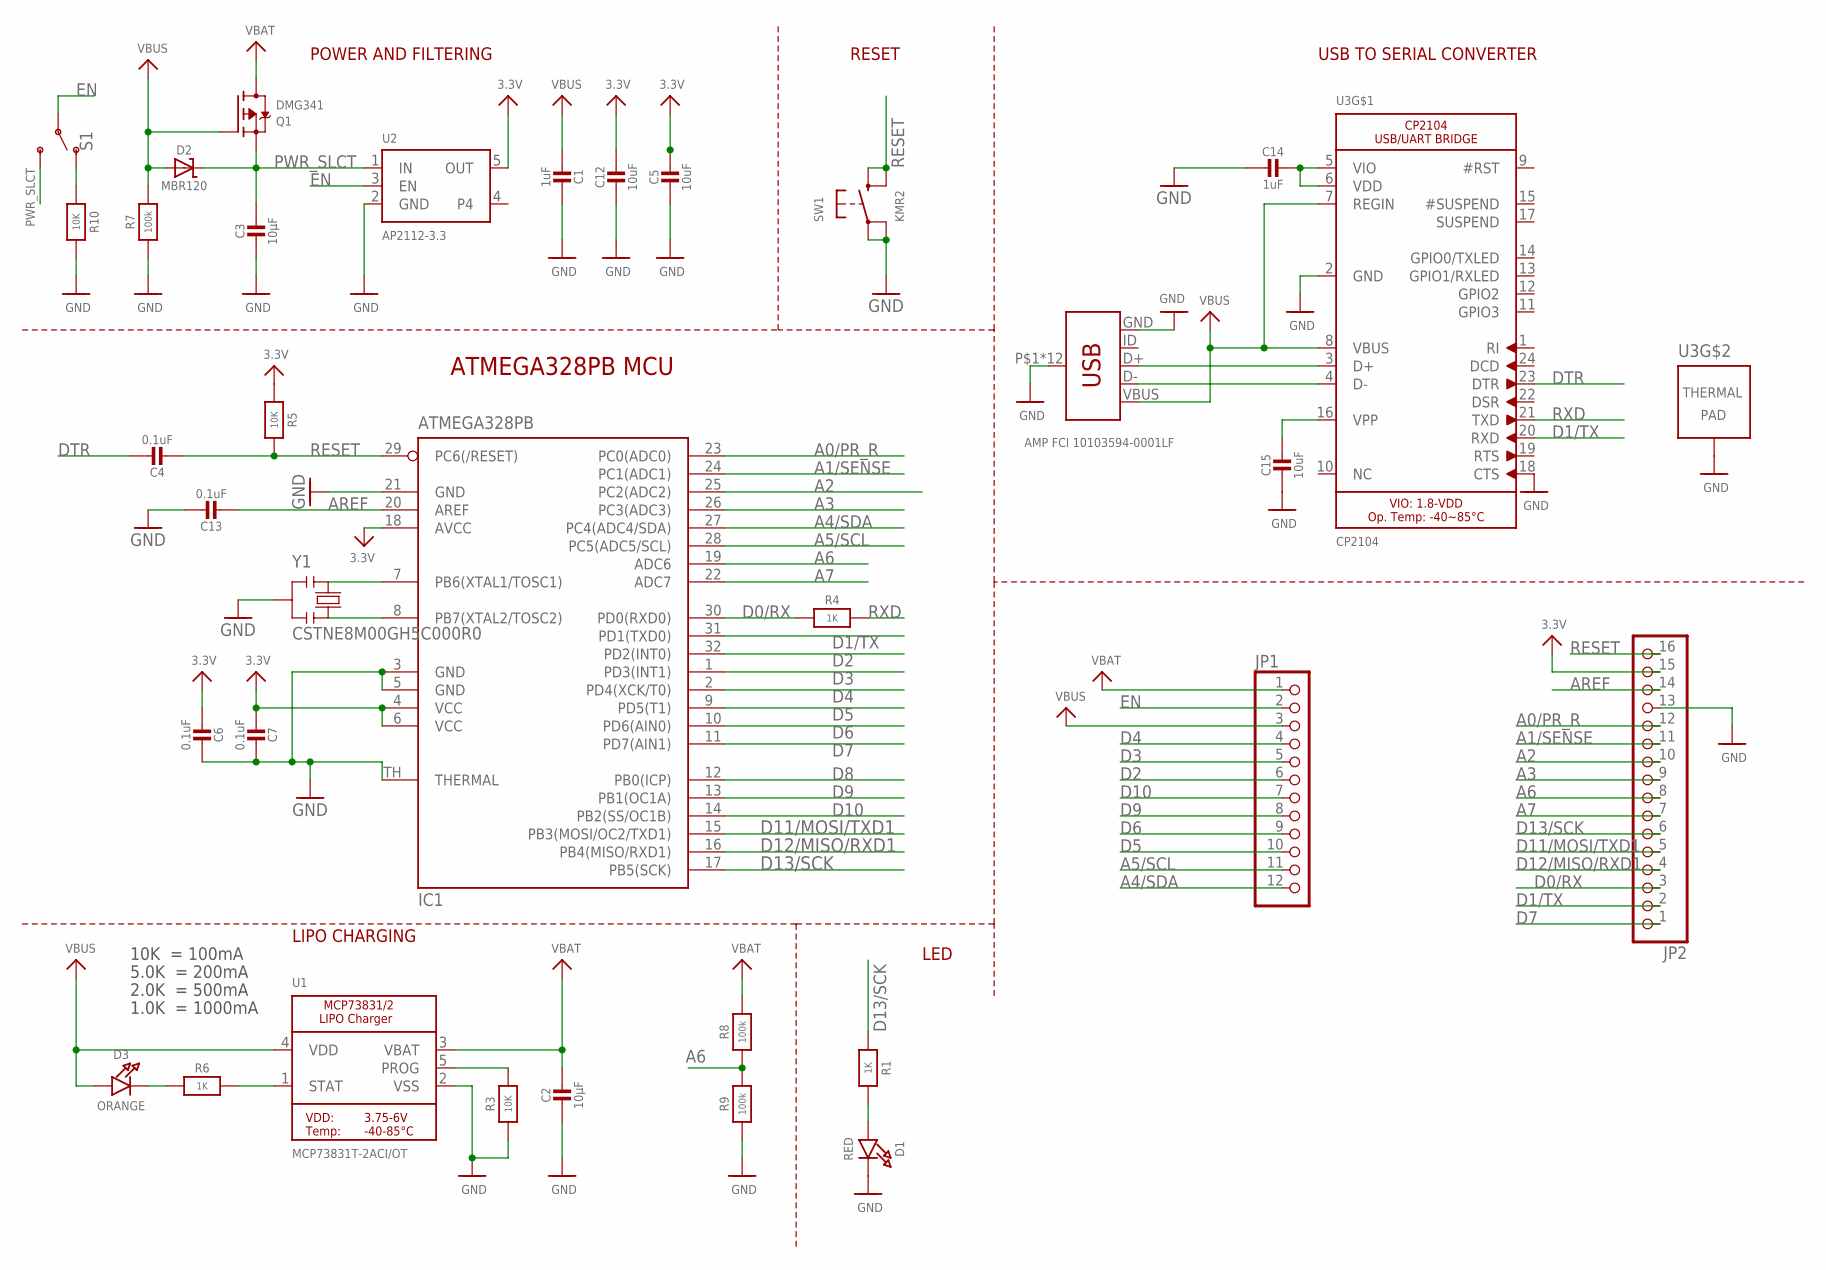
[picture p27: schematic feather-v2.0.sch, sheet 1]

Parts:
C1, C14: 1uF; _0603MP
C2, C3: 10µF; _0603MP
C4, C6, C7, C13: 0.1uF; _0603MP
C5, C12, C15: 10uF; _0603MP
D1: RED; CHIPLED_0603_NOOUTLINE
D2: MBR120; SOD-323
D3: ORANGE; CHIPLED_0603_NOOUTLINE
IC1: ATMEGA328PB; MLF32-TH
JP1: HEADER-1X12; 1X12_ROUND
JP2: HEADER-1X16ROUND; 1X16_ROUND
Q1: DMG341; SOT23-R
R1, R4, R6: 1K; _0603MP
R3, R5, R10: 10K; _0603MP
R7, R8, R9: 100k; _0603MP
S1: SWITCH-SPDT-SMD-RIGHT-ANGLE; SWITCH_SPST_SMD_A
SW1: KMR2; BTN_KMR2_4.6X2.8
U1: MCP73831T-2ACI/OT; SOT23-5
U2: AP2112-3.3; SOT23-5
U3: CP2104; QFN24_4MM_SMSC
X1: AMP FCI 10103594-0001LF; USB-MICROB-PTH
Y1: CSTNE8M00GH5C000R0; RESONATOR

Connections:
3.3V: C5.1, C6.2, C7.2, C12.1, IC1.4 (VCC), IC1.6 (VCC), IC1.18 (AVCC), JP2.15, R5.2, U2.5 (OUT); also elsewhere on the board
A0/PR_R: IC1.23 (PC0(ADC0)), JP2.12; also elsewhere on the board
A1/SENSE: IC1.24 (PC1(ADC1)), JP2.11; also elsewhere on the board
A2: IC1.25 (PC2(ADC2)), JP2.10; also elsewhere on the board
A3: IC1.26 (PC3(ADC3)), JP2.9; also elsewhere on the board
A4/SDA: IC1.27 (PC4(ADC4/SDA)), JP1.12; also elsewhere on the board
A5/SCL: IC1.28 (PC5(ADC5/SCL)), JP1.11; also elsewhere on the board
A6: IC1.19 (ADC6), JP2.8, R8.1, R9.2
A7: IC1.22 (ADC7), JP2.7; also elsewhere on the board
AREF: C13.2, IC1.20 (AREF), JP2.14
D0/RX: IC1.30 (PD0(RXD0)), JP2.3, R4.1
D1/TX: IC1.31 (PD1(TXD0)), JP2.2, U3.20 (RXD)
D2: IC1.32 (PD2(INT0)), JP1.6
D3: IC1.1 (PD3(INT1)), JP1.5
D4: IC1.2 (PD4(XCK/T0)), JP1.4
D5: IC1.9 (PD5(T1)), JP1.10
D6: IC1.10 (PD6(AIN0)), JP1.9
D7: IC1.11 (PD7(AIN1)), JP2.1; also elsewhere on the board
D8: IC1.12 (PB0(ICP))
D9: IC1.13 (PB1(OC1A)), JP1.8; also elsewhere on the board
D10: IC1.14 (PB2(SS/OC1B)), JP1.7; also elsewhere on the board
D11/MOSI/TXD1: IC1.15 (PB3(MOSI/OC2/TXD1)), JP2.5; also elsewhere on the board
D12/MISO/RXD1: IC1.16 (PB4(MISO/RXD1)), JP2.4; also elsewhere on the board
D13/SCK: IC1.17 (PB5(SCK)), JP2.6, R1.1
DTR: C4.1, U3.23 (DTR)
EN: JP1.2, S1.2, U2.3 (EN)
GND: C1.1, C2.2, C3.2, C5.2, C6.1, C7.1, C12.2, C13.1, C14.2, C15.2, D1.C, IC1.3 (GND), IC1.5 (GND), IC1.21 (GND), IC1.TH (THERMAL), JP2.13, R3.1, R7.1, R9.1, R10.1, SW1.A, SW1.A' (P1), U1.2 (VSS), U2.2 (GND), U3.2 (GND), U3.18 (CTS), U3.THERM (TP), X1.GND, X1.P$1 (SHIELD), X1.P$2 (SHIELD), X1.P$3 (SHIELD), X1.P$4 (SHIELD), X1.P$6 (SHIELD), X1.P$8 (SHIELD), X1.P$10 (SHIELD), X1.P$12 (SHIELD), X1.SHEILD2 (SHIELD), X1.SHIELD, X1.SHIELD3 (SHIELD), X1.SHIELD4 (SHIELD), Y1.2; also elsewhere on the board
unnamed: D3.C, R6.1
unnamed: U3.3 (D+), X1.D+
unnamed: R6.2, U1.1 (STAT)
unnamed: R3.2, U1.5 (PROG)
unnamed: D1.A, R1.2
unnamed: U3.4 (D-), X1.D-
unnamed: R10.2, S1.1 (O)
unnamed: IC1.8 (PB7(XTAL2/TOSC2)), Y1.3
unnamed: C14.1, U3.5 (VIO), U3.6 (VDD)
unnamed: IC1.7 (PB6(XTAL1/TOSC1)), Y1.1
unnamed: C15.1, U3.16 (VPP)
PWR_SLCT: C3.1, D2.C, Q1.2 (S), S1.3 (S), U2.1 (IN)
RESET: C4.2, IC1.29 (PC6(/RESET)), JP2.16, R5.1, SW1.B (S), SW1.B' (S1)
RXD: R4.2, U3.21 (TXD)
VBAT: C2.1, JP1.1, Q1.3 (D), R8.2, U1.3 (VBAT); also elsewhere on the board
VBUS: C1.2, D2.A, D3.A, JP1.3, Q1.1 (G), R7.2, U1.4 (VDD), U3.7 (REGIN), U3.8 (VBUS), X1.VBUS

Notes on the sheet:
POWER AND FILTERING
RESET
10K = 100mA
5.0K = 200mA
2.0K = 500mA
1.0K = 1000mA
USB TO SERIAL CONVERTER
LIPO CHARGING
LED
ATMEGA328PB MCU

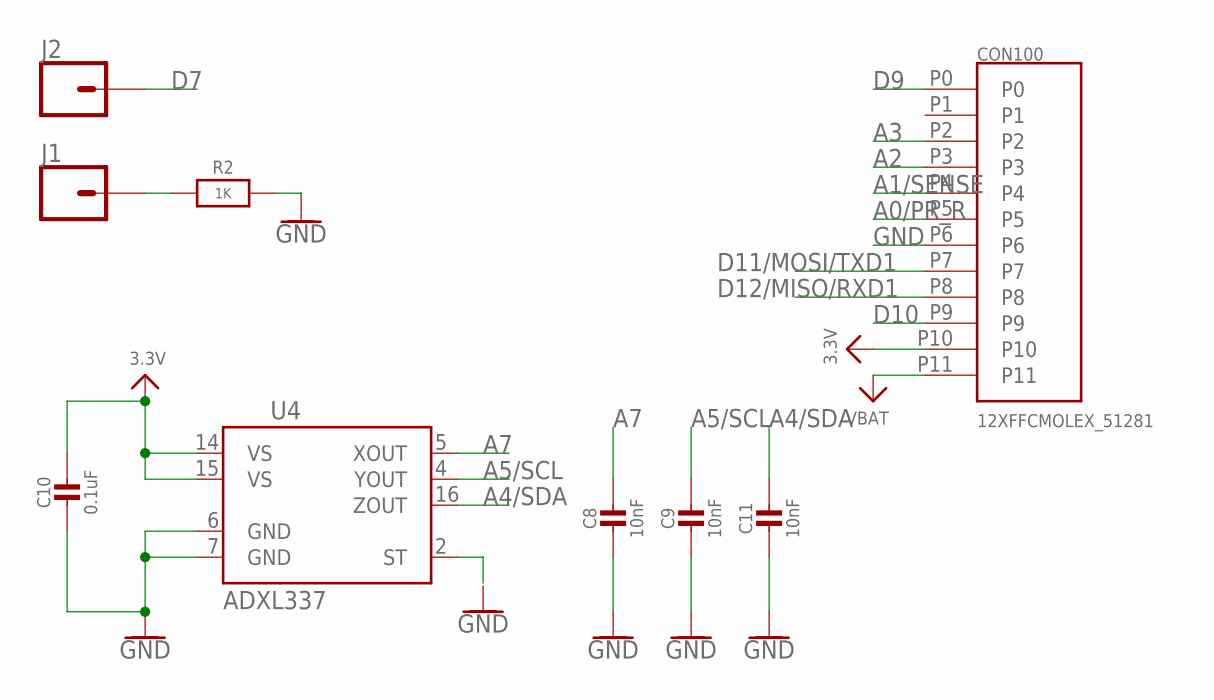
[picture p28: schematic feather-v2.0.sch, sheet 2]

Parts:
C8, C9, C11: 10nF; _0603MP
C10: 0.1uF; _0603MP
CON100: 12XFFCMOLEX_51281; MOLEX_51281-1294
J1, J2: CONN_01PTH_NO_SILK_YES_STOP; 1X01_NO_SILK
R2: 1K; _0603MP
U4: ADXL337; LFCSP_LQ-16

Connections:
3.3V: C10.1, CON100.P10, U4.14 (VS), U4.15 (VS); also elsewhere on the board
A0/PR_R: CON100.P5; also elsewhere on the board
A1/SENSE: CON100.P4; also elsewhere on the board
A2: CON100.P3; also elsewhere on the board
A3: CON100.P2; also elsewhere on the board
A4/SDA: C11.1, U4.16 (ZOUT); also elsewhere on the board
A5/SCL: C9.1, U4.4 (YOUT); also elsewhere on the board
A7: C8.1, U4.5 (XOUT); also elsewhere on the board
D7: J2.1; also elsewhere on the board
D9: CON100.P0; also elsewhere on the board
D10: CON100.P9; also elsewhere on the board
D11/MOSI/TXD1: CON100.P7; also elsewhere on the board
D12/MISO/RXD1: CON100.P8; also elsewhere on the board
GND: C8.2, C9.2, C10.2, C11.2, CON100.P6, R2.2, U4.6 (GND), U4.7 (GND); also elsewhere on the board
unnamed: J1.1, R2.1
VBAT: CON100.P11; also elsewhere on the board

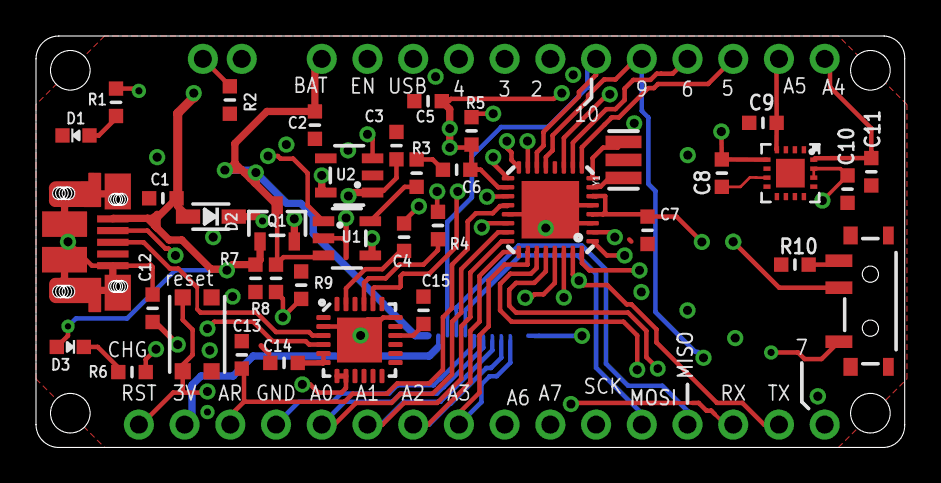
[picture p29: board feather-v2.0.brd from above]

Board: 4 copper layers, 48.3 x 22.9 mm, 43 parts (1 on the bottom side), 43 nets.

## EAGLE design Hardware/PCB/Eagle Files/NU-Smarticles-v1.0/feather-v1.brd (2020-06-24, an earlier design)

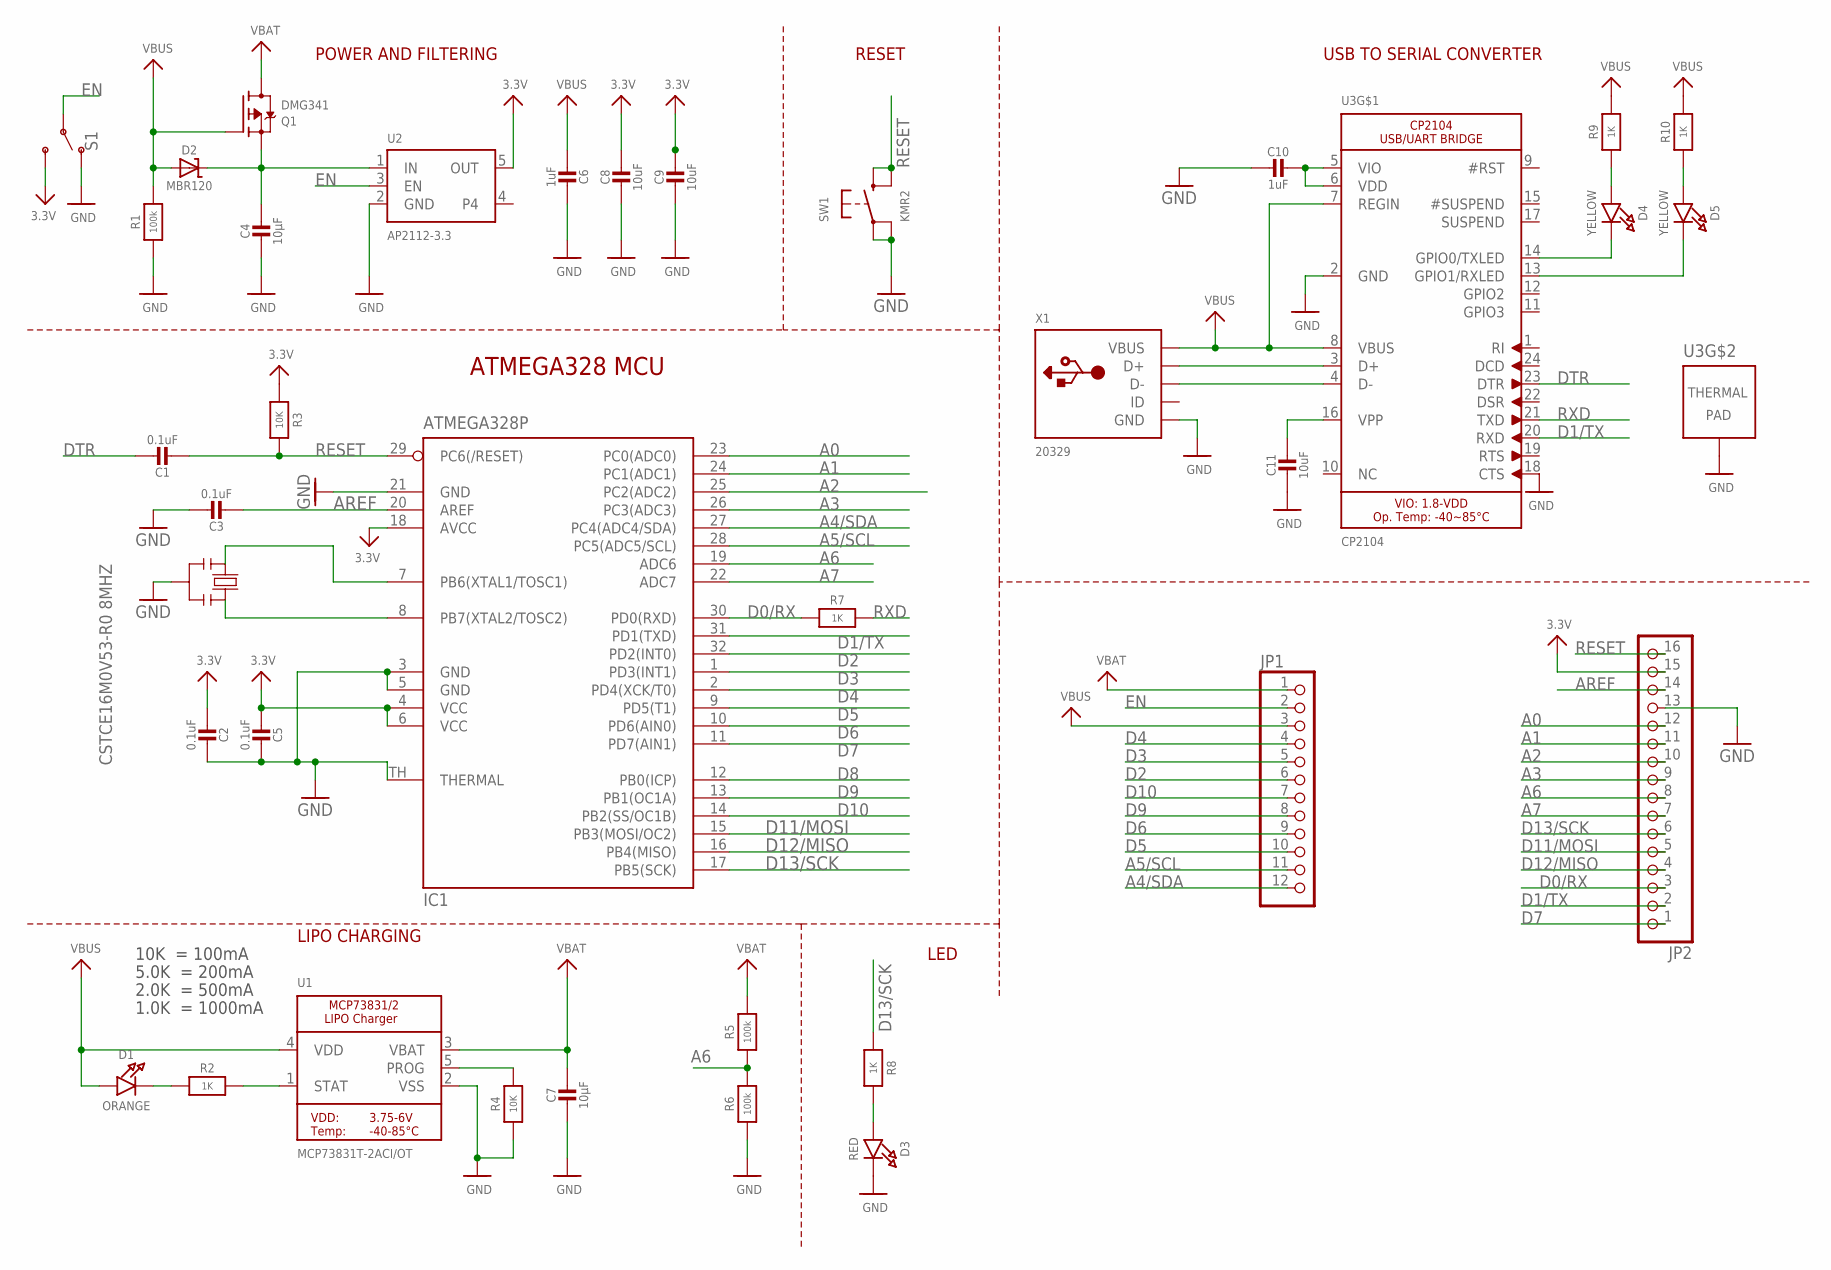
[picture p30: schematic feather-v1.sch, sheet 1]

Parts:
C1, C2, C3, C5: 0.1uF; _0603MP
C4, C7: 10µF; _0603MP
C6, C10: 1uF; _0603MP
C8, C9, C11: 10uF; _0603MP
D1: ORANGE; CHIPLED_0603_NOOUTLINE
D2: MBR120; SOD-523
D3: RED; CHIPLED_0603_NOOUTLINE
D4, D5: YELLOW; CHIPLED_0603_NOOUTLINE
IC1: ATMEGA328P; MLF32-TH
JP1: HEADER-1X12; 1X12_ROUND
JP2: HEADER-1X16ROUND; 1X16_ROUND
Q1: DMG341; SOT23-R
R1, R5, R6: 100k; _0603MP
R2, R7, R8, R9, R10: 1K; _0603MP
R3, R4: 10K; _0603MP
S1: SWITCH-SPDT-SMD-RIGHT-ANGLE; SWITCH_SPST_SMD_A
SW1: KMR2; BTN_KMR2_4.6X2.8
U1: MCP73831T-2ACI/OT; SOT23-5
U2: AP2112-3.3; SOT23-5
U3: CP2104; QFN24_4MM_SMSC
X1: 20329; 4UCONN_20329_V2
Y1: CSTCE16M0V53-R0 8MHZ; RESONATOR

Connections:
3.3V: C2.2, C5.2, C8.1, C9.1, IC1.4 (VCC), IC1.6 (VCC), IC1.18 (AVCC), JP2.15, R3.2, S1.3 (S), U2.5 (OUT); also elsewhere on the board
A0: IC1.23 (PC0(ADC0)), JP2.12; also elsewhere on the board
A1: IC1.24 (PC1(ADC1)), JP2.11; also elsewhere on the board
A2: IC1.25 (PC2(ADC2)), JP2.10; also elsewhere on the board
A3: IC1.26 (PC3(ADC3)), JP2.9; also elsewhere on the board
A4/SDA: IC1.27 (PC4(ADC4/SDA)), JP1.12
A5/SCL: IC1.28 (PC5(ADC5/SCL)), JP1.11
A6: IC1.19 (ADC6), JP2.8, R5.1, R6.2
A7: IC1.22 (ADC7), JP2.7
AREF: C3.2, IC1.20 (AREF), JP2.14
D0/RX: IC1.30 (PD0(RXD)), JP2.3, R7.1
D1/TX: IC1.31 (PD1(TXD)), JP2.2, U3.20 (RXD)
D2: IC1.32 (PD2(INT0)), JP1.6; also elsewhere on the board
D3: IC1.1 (PD3(INT1)), JP1.5; also elsewhere on the board
D4: IC1.2 (PD4(XCK/T0)), JP1.4; also elsewhere on the board
D5: IC1.9 (PD5(T1)), JP1.10
D6: IC1.10 (PD6(AIN0)), JP1.9
D7: IC1.11 (PD7(AIN1)), JP2.1; also elsewhere on the board
D8: IC1.12 (PB0(ICP))
D9: IC1.13 (PB1(OC1A)), JP1.8
D10: IC1.14 (PB2(SS/OC1B)), JP1.7; also elsewhere on the board
D11/MOSI: IC1.15 (PB3(MOSI/OC2)), JP2.5
D12/MISO: IC1.16 (PB4(MISO)), JP2.4
D13/SCK: IC1.17 (PB5(SCK)), JP2.6, R8.1
DTR: C1.1, U3.23 (DTR)
EN: JP1.2, S1.2, U2.3 (EN)
GND: C2.1, C3.1, C4.2, C5.1, C6.1, C7.2, C8.2, C9.2, C10.2, C11.2, D3.C, IC1.3 (GND), IC1.5 (GND), IC1.21 (GND), IC1.TH (THERMAL), JP2.13, R1.1, R4.1, R6.1, S1.1 (O), SW1.A, SW1.A' (P1), U1.2 (VSS), U2.2 (GND), U3.2 (GND), U3.18 (CTS), U3.THERM (TP), X1.BASE@1 (GND), X1.BASE@2 (GND), X1.GND, X1.SPRT@1 (GND), X1.SPRT@2 (GND), X1.SPRT@3 (GND), X1.SPRT@4 (GND), Y1.2; also elsewhere on the board
unnamed: D1.C, R2.1
unnamed: U3.3 (D+), X1.D+
unnamed: R2.2, U1.1 (STAT)
unnamed: R4.2, U1.5 (PROG)
unnamed: D3.A, R8.2
unnamed: U3.4 (D-), X1.D-
unnamed: C4.1, D2.K (C), Q1.2 (S), U2.1 (IN)
unnamed: D5.A, R10.1
unnamed: D4.A, R9.1
unnamed: C10.1, U3.5 (VIO), U3.6 (VDD)
unnamed: C11.1, U3.16 (VPP)
RESET: C1.2, IC1.29 (PC6(/RESET)), JP2.16, R3.1, SW1.B (S), SW1.B' (S1)
RXD: R7.2, U3.21 (TXD)
RXLED: D5.C, U3.13 (GPIO1/RXLED)
TXLED: D4.C, U3.14 (GPIO0/TXLED)
VBAT: C7.1, JP1.1, Q1.3 (D), R5.2, U1.3 (VBAT); also elsewhere on the board
VBUS: C6.2, D1.A, D2.A, JP1.3, Q1.1 (G), R1.2, R9.2, R10.2, U1.4 (VDD), U3.7 (REGIN), U3.8 (VBUS), X1.VBUS
XTAL1: IC1.8 (PB7(XTAL2/TOSC2)), Y1.3
XTAL2: IC1.7 (PB6(XTAL1/TOSC1)), Y1.1

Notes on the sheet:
POWER AND FILTERING
RESET
10K = 100mA
5.0K = 200mA
2.0K = 500mA
1.0K = 1000mA
USB TO SERIAL CONVERTER
LIPO CHARGING
LED
ATMEGA328 MCU

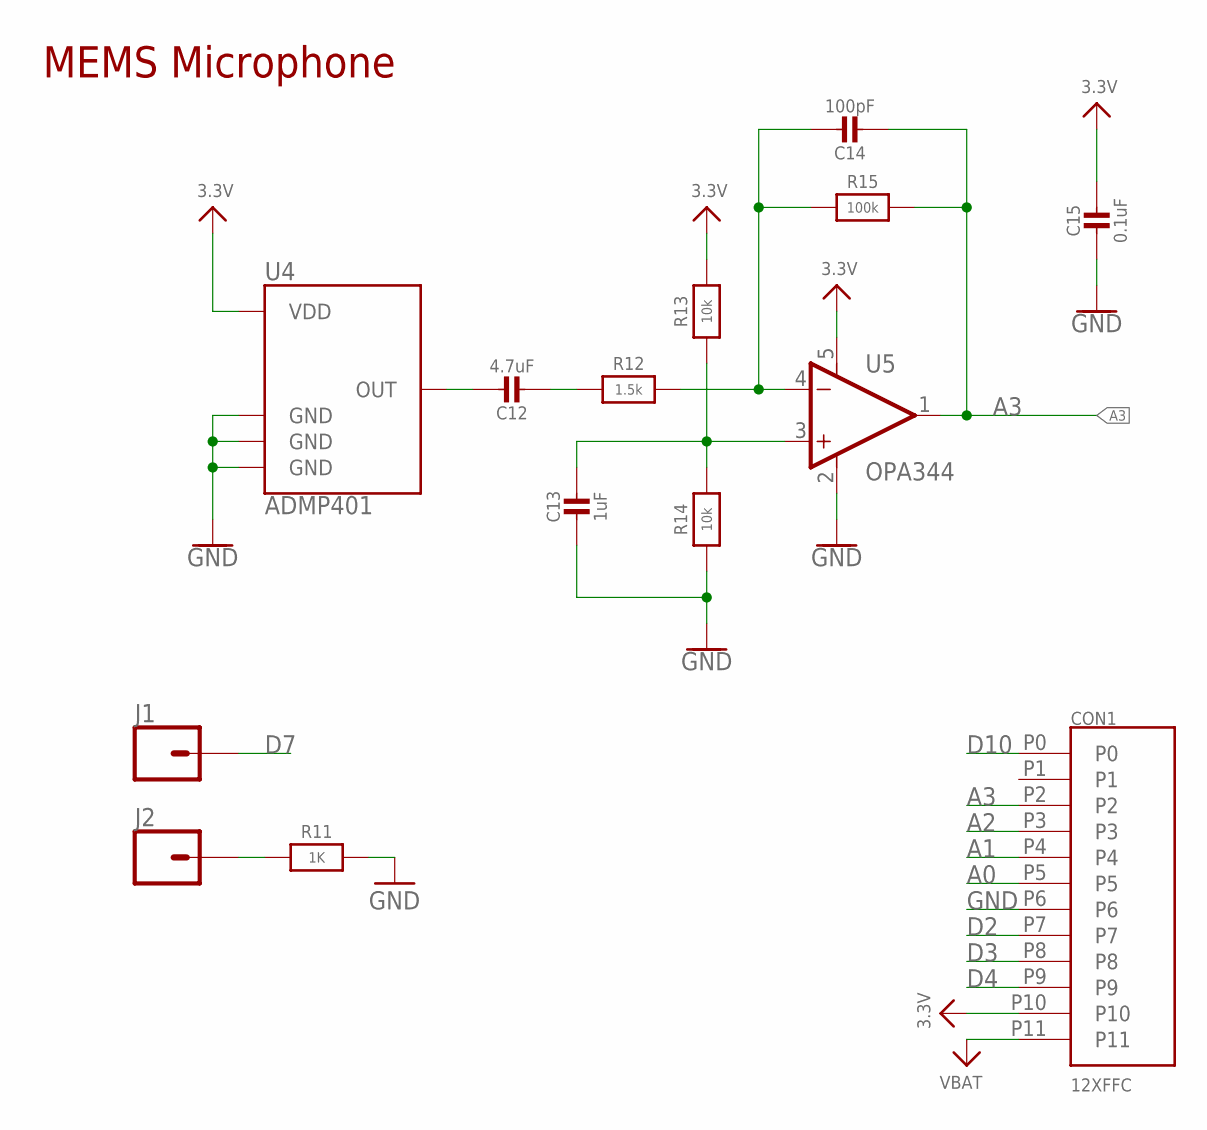
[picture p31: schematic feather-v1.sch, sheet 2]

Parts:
C12: 4.7uF; _0603MP
C13: 1uF; _0603MP
C14: 100pF; _0603MP
C15: 0.1uF; _0603MP
CON1: 12XFFC; 15166-0117
J1, J2: CONN_01PTH_NO_SILK_YES_STOP; 1X01_NO_SILK
R11: 1K; _0603MP
R12: 1.5k; _0603MP
R13, R14: 10k; _0603MP
R15: 100k; _0603MP
U4: ADMP401
U5: OPA344; SOT23-5

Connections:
3.3V: C15.1, CON1.P10, R13.2, U4.5 (VDD), U5.5 (V+); also elsewhere on the board
A0: CON1.P5; also elsewhere on the board
A1: CON1.P4; also elsewhere on the board
A2: CON1.P3; also elsewhere on the board
A3: C14.2, CON1.P2, R15.2, U5.1 (OUT); also elsewhere on the board
D2: CON1.P7; also elsewhere on the board
D3: CON1.P8; also elsewhere on the board
D4: CON1.P9; also elsewhere on the board
D7: J1.1; also elsewhere on the board
D10: CON1.P0; also elsewhere on the board
GND: C13.2, C15.2, CON1.P6, R11.2, R14.1, U4.2 (GND), U4.4 (GND), U4.6 (GND), U5.2 (V-); also elsewhere on the board
unnamed: J2.1, R11.1
unnamed: C12.1, U4.1 (OUT)
unnamed: C14.1, R12.2, R15.1, U5.4 (-IN)
unnamed: C12.2, R12.1
unnamed: C13.1, R13.1, R14.2, U5.3 (+IN)
VBAT: CON1.P11; also elsewhere on the board

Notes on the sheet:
MEMS Microphone

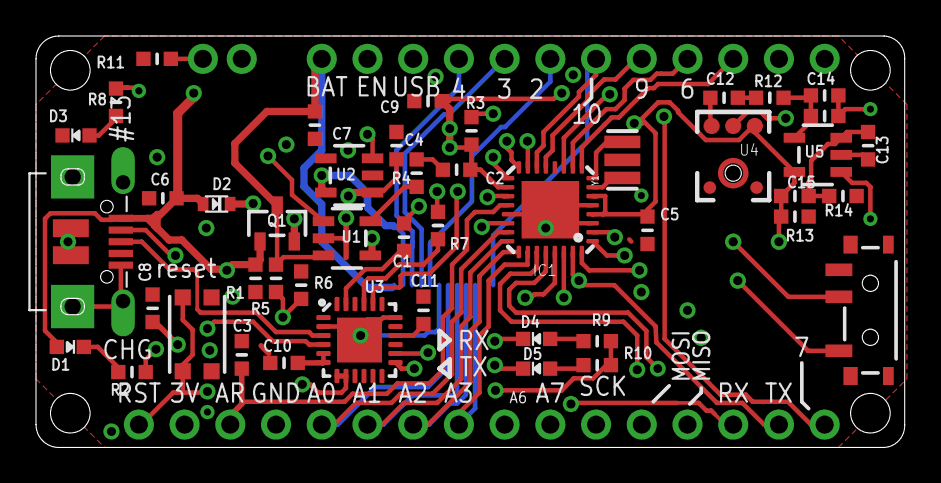
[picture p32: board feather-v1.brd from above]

Board: 4 copper layers, 48.3 x 22.9 mm, 51 parts (1 on the bottom side), 50 nets.

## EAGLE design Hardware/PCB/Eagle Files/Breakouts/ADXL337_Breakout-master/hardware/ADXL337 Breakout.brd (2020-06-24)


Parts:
C1, C2, C3: 10nF; 0603-CAP
C4: 0.1uF; 0603-CAP
FID1, FID2: FIDUCIAL1X2; FIDUCIAL-1X2
FRAME1: FRAME-LETTER; CREATIVE_COMMONS
JP1: M06SIP; 1X06
LOGO1: SFE_LOGO_FLAME.1_INCH; SFE_LOGO_FLAME_.1
LOGO2: OSHW-LOGOS; OSHW-LOGO-S
LOGO3: SFE_LOGO_NAME_FLAME.1_INCH; SFE_LOGO_NAME_FLAME_.1
STANDOFF1: STAND-OFF
U1: ADXL337; LFCSP_LQ-16

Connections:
3.3V: C4.1, JP1.2, U1.14 (VS), U1.15 (VS)
GND: C1.2, C2.2, C3.2, C4.2, JP1.1, U1.6 (GND), U1.7 (GND)
ST: JP1.6, U1.2 (ST)
X: C1.1, JP1.3, U1.5 (XOUT)
Y: C2.1, JP1.4, U1.4 (YOUT)
Z: C3.1, JP1.5, U1.16 (ZOUT)

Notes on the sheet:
Jordan McConnell
v10



Board: 2 copper layers, 17.8 x 17.8 mm, 13 parts (2 on the bottom side), 6 nets.

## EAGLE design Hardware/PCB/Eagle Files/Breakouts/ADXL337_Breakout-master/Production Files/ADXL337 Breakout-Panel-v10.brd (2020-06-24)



Board: 2 copper layers, 122.9 x 122.9 mm, 435 parts (72 on the bottom side), 216 nets.

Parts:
C1, C2, C3, C5, C6, C7, C9, C10, C11, C13, C14, C15, C17, C18, C19, C21, C22, C23, C25, C26, C27, C29, C30, C31, C33, C34, C35, C37, C38, C39, C41, C42, C43, C45, C46, C47, C49, C50, C51, C53, C54, C55, C57, C58, C59, C61, C62, C63, C65, C66, C67, C69, C70, C71, C73, C74, C75, C77, C78, C79, C81, C82, C83, C85, C86, C87, C89, C90, C91, C93, C94, C95, C97, C98, C99, C101, C102, C103, C105, C106, C107, C109, C110, C111, C113, C114, C115, C117, C118, C119, C121, C122, C123, C125, C126, C127, C129, C130, C131, C133, C134, C135, C137, C138, C139, C141, C142, C143: 10nF; 0603-CAP
C4, C8, C12, C16, C20, C24, C28, C32, C36, C40, C44, C48, C52, C56, C60, C64, C68, C72, C76, C80, C84, C88, C92, C96, C100, C104, C108, C112, C116, C120, C124, C128, C132, C136, C140, C144: 0.1uF; 0603-CAP
E$1: FIDUCIAL-1.5X3
E$4, E$6: FIDUCIAL-1X2
FID1, FID2, FID3, FID4, FID5, FID6, FID7, FID8, FID9, FID10, FID11, FID12, FID13, FID14, FID15, FID16, FID17, FID18, FID19, FID20, FID21, FID22, FID23, FID24, FID25, FID26, FID27, FID28, FID29, FID30, FID31, FID32, FID33, FID34, FID35, FID36, FID37, FID38, FID39, FID40, FID41, FID42, FID43, FID44, FID45, FID46, FID47, FID48, FID49, FID50, FID51, FID52, FID53, FID54, FID55, FID56, FID57, FID58, FID59, FID60, FID61, FID62, FID63, FID64, FID65, FID66, FID67, FID68, FID69, FID70, FID71, FID72: FIDUCIAL1X2; FIDUCIAL-1X2
JP1, JP2, JP3, JP4, JP5, JP6, JP7, JP8, JP9, JP10, JP11, JP12, JP13, JP14, JP15, JP16, JP17, JP18, JP19, JP20, JP21, JP22, JP23, JP24, JP25, JP26, JP27, JP28, JP29, JP30, JP31, JP32, JP33, JP34, JP35, JP36: 1X06
LOGO1, LOGO4, LOGO7, LOGO10, LOGO13, LOGO16, LOGO19, LOGO22, LOGO25, LOGO28, LOGO31, LOGO34, LOGO37, LOGO40, LOGO43, LOGO46, LOGO49, LOGO52, LOGO55, LOGO58, LOGO61, LOGO64, LOGO67, LOGO70, LOGO73, LOGO76, LOGO79, LOGO82, LOGO85, LOGO88, LOGO91, LOGO94, LOGO97, LOGO100, LOGO103, LOGO106: SFE_LOGO_FLAME.1_INCH; SFE_LOGO_FLAME_.1
LOGO2, LOGO5, LOGO8, LOGO11, LOGO14, LOGO17, LOGO20, LOGO23, LOGO26, LOGO29, LOGO32, LOGO35, LOGO38, LOGO41, LOGO44, LOGO47, LOGO50, LOGO53, LOGO56, LOGO59, LOGO62, LOGO65, LOGO68, LOGO71, LOGO74, LOGO77, LOGO80, LOGO83, LOGO86, LOGO89, LOGO92, LOGO95, LOGO98, LOGO101, LOGO104, LOGO107: OSHW-LOGOS; OSHW-LOGO-S
LOGO3, LOGO6, LOGO9, LOGO12, LOGO15, LOGO18, LOGO21, LOGO24, LOGO27, LOGO30, LOGO33, LOGO36, LOGO39, LOGO42, LOGO45, LOGO48, LOGO51, LOGO54, LOGO57, LOGO60, LOGO63, LOGO66, LOGO69, LOGO72, LOGO75, LOGO78, LOGO81, LOGO84, LOGO87, LOGO90, LOGO93, LOGO96, LOGO99, LOGO102, LOGO105, LOGO108: SFE_LOGO_NAME_FLAME.1_INCH; SFE_LOGO_NAME_FLAME_.1
STANDOFF1, STANDOFF2, STANDOFF3, STANDOFF4, STANDOFF5, STANDOFF6, STANDOFF7, STANDOFF8, STANDOFF9, STANDOFF10, STANDOFF11, STANDOFF12, STANDOFF13, STANDOFF14, STANDOFF15, STANDOFF16, STANDOFF17, STANDOFF18, STANDOFF19, STANDOFF20, STANDOFF21, STANDOFF22, STANDOFF23, STANDOFF24, STANDOFF25, STANDOFF26, STANDOFF27, STANDOFF28, STANDOFF29, STANDOFF30, STANDOFF31, STANDOFF32, STANDOFF33, STANDOFF34, STANDOFF35, STANDOFF36: STAND-OFF
U1, U2, U3, U4, U5, U6, U7, U8, U9, U10, U11, U12, U13, U14, U15, U16, U17, U18, U19, U20, U21, U22, U23, U24, U25, U26, U27, U28, U29, U30, U31, U32, U33, U34, U35, U36: ADXL337; LFCSP_LQ-16

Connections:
3.3V: C4.1, JP1.2, U1.14, U1.15
3.3V1: C8.1, JP2.2, U2.14, U2.15
3.3V2: C12.1, JP3.2, U3.14, U3.15
3.3V3: C16.1, JP4.2, U4.14, U4.15
3.3V4: C20.1, JP5.2, U5.14, U5.15
3.3V5: C24.1, JP6.2, U6.14, U6.15
3.3V6: C28.1, JP7.2, U7.14, U7.15
3.3V7: C32.1, JP8.2, U8.14, U8.15
3.3V8: C36.1, JP9.2, U9.14, U9.15
3.3V9: C40.1, JP10.2, U10.14, U10.15
3.3V10: C44.1, JP11.2, U11.14, U11.15
3.3V11: C48.1, JP12.2, U12.14, U12.15
3.3V12: C52.1, JP13.2, U13.14, U13.15
3.3V13: C56.1, JP14.2, U14.14, U14.15
3.3V14: C60.1, JP15.2, U15.14, U15.15
3.3V15: C64.1, JP16.2, U16.14, U16.15
3.3V16: C68.1, JP17.2, U17.14, U17.15
3.3V17: C72.1, JP18.2, U18.14, U18.15
3.3V18: C76.1, JP19.2, U19.14, U19.15
3.3V19: C80.1, JP20.2, U20.14, U20.15
3.3V20: C84.1, JP21.2, U21.14, U21.15
3.3V21: C88.1, JP22.2, U22.14, U22.15
3.3V22: C92.1, JP23.2, U23.14, U23.15
3.3V23: C96.1, JP24.2, U24.14, U24.15
3.3V24: C100.1, JP25.2, U25.14, U25.15
3.3V25: C104.1, JP26.2, U26.14, U26.15
3.3V26: C108.1, JP27.2, U27.14, U27.15
3.3V27: C112.1, JP28.2, U28.14, U28.15
3.3V28: C116.1, JP29.2, U29.14, U29.15
3.3V29: C120.1, JP30.2, U30.14, U30.15
3.3V30: C124.1, JP31.2, U31.14, U31.15
3.3V31: C128.1, JP32.2, U32.14, U32.15
3.3V32: C132.1, JP33.2, U33.14, U33.15
3.3V33: C136.1, JP34.2, U34.14, U34.15
3.3V34: C140.1, JP35.2, U35.14, U35.15
3.3V35: C144.1, JP36.2, U36.14, U36.15
GND: C1.2, C2.2, C3.2, C4.2, JP1.1, U1.6, U1.7
GND1: C5.2, C6.2, C7.2, C8.2, JP2.1, U2.6, U2.7
GND2: C9.2, C10.2, C11.2, C12.2, JP3.1, U3.6, U3.7
GND3: C13.2, C14.2, C15.2, C16.2, JP4.1, U4.6, U4.7
GND4: C17.2, C18.2, C19.2, C20.2, JP5.1, U5.6, U5.7
GND5: C21.2, C22.2, C23.2, C24.2, JP6.1, U6.6, U6.7
GND6: C25.2, C26.2, C27.2, C28.2, JP7.1, U7.6, U7.7
GND7: C29.2, C30.2, C31.2, C32.2, JP8.1, U8.6, U8.7
GND8: C33.2, C34.2, C35.2, C36.2, JP9.1, U9.6, U9.7
GND9: C37.2, C38.2, C39.2, C40.2, JP10.1, U10.6, U10.7
GND10: C41.2, C42.2, C43.2, C44.2, JP11.1, U11.6, U11.7
GND11: C45.2, C46.2, C47.2, C48.2, JP12.1, U12.6, U12.7
GND12: C49.2, C50.2, C51.2, C52.2, JP13.1, U13.6, U13.7
GND13: C53.2, C54.2, C55.2, C56.2, JP14.1, U14.6, U14.7
GND14: C57.2, C58.2, C59.2, C60.2, JP15.1, U15.6, U15.7
GND15: C61.2, C62.2, C63.2, C64.2, JP16.1, U16.6, U16.7
GND16: C65.2, C66.2, C67.2, C68.2, JP17.1, U17.6, U17.7
GND17: C69.2, C70.2, C71.2, C72.2, JP18.1, U18.6, U18.7
GND18: C73.2, C74.2, C75.2, C76.2, JP19.1, U19.6, U19.7
GND19: C77.2, C78.2, C79.2, C80.2, JP20.1, U20.6, U20.7
GND20: C81.2, C82.2, C83.2, C84.2, JP21.1, U21.6, U21.7
GND21: C85.2, C86.2, C87.2, C88.2, JP22.1, U22.6, U22.7
GND22: C89.2, C90.2, C91.2, C92.2, JP23.1, U23.6, U23.7
GND23: C93.2, C94.2, C95.2, C96.2, JP24.1, U24.6, U24.7
GND24: C97.2, C98.2, C99.2, C100.2, JP25.1, U25.6, U25.7
GND25: C101.2, C102.2, C103.2, C104.2, JP26.1, U26.6, U26.7
GND26: C105.2, C106.2, C107.2, C108.2, JP27.1, U27.6, U27.7
GND27: C109.2, C110.2, C111.2, C112.2, JP28.1, U28.6, U28.7
GND28: C113.2, C114.2, C115.2, C116.2, JP29.1, U29.6, U29.7
GND29: C117.2, C118.2, C119.2, C120.2, JP30.1, U30.6, U30.7
GND30: C121.2, C122.2, C123.2, C124.2, JP31.1, U31.6, U31.7
GND31: C125.2, C126.2, C127.2, C128.2, JP32.1, U32.6, U32.7
GND32: C129.2, C130.2, C131.2, C132.2, JP33.1, U33.6, U33.7
GND33: C133.2, C134.2, C135.2, C136.2, JP34.1, U34.6, U34.7
GND34: C137.2, C138.2, C139.2, C140.2, JP35.1, U35.6, U35.7
GND35: C141.2, C142.2, C143.2, C144.2, JP36.1, U36.6, U36.7
ST: JP1.6, U1.2
ST1: JP2.6, U2.2
ST2: JP3.6, U3.2
ST3: JP4.6, U4.2
ST4: JP5.6, U5.2
ST5: JP6.6, U6.2
ST6: JP7.6, U7.2
ST7: JP8.6, U8.2
ST8: JP9.6, U9.2
ST9: JP10.6, U10.2
ST10: JP11.6, U11.2
ST11: JP12.6, U12.2
ST12: JP13.6, U13.2
ST13: JP14.6, U14.2
ST14: JP15.6, U15.2
ST15: JP16.6, U16.2
ST16: JP17.6, U17.2
ST17: JP18.6, U18.2
ST18: JP19.6, U19.2
ST19: JP20.6, U20.2
ST20: JP21.6, U21.2
ST21: JP22.6, U22.2
ST22: JP23.6, U23.2
ST23: JP24.6, U24.2
ST24: JP25.6, U25.2
ST25: JP26.6, U26.2
ST26: JP27.6, U27.2
ST27: JP28.6, U28.2
ST28: JP29.6, U29.2
ST29: JP30.6, U30.2
ST30: JP31.6, U31.2
ST31: JP32.6, U32.2
ST32: JP33.6, U33.2
ST33: JP34.6, U34.2
ST34: JP35.6, U35.2
ST35: JP36.6, U36.2
X: C1.1, JP1.3, U1.5
X1: C5.1, JP2.3, U2.5
X2: C9.1, JP3.3, U3.5
X3: C13.1, JP4.3, U4.5
X4: C17.1, JP5.3, U5.5
X5: C21.1, JP6.3, U6.5
X6: C25.1, JP7.3, U7.5
X7: C29.1, JP8.3, U8.5
X8: C33.1, JP9.3, U9.5
X9: C37.1, JP10.3, U10.5
X10: C41.1, JP11.3, U11.5
X11: C45.1, JP12.3, U12.5
X12: C49.1, JP13.3, U13.5
X13: C53.1, JP14.3, U14.5
X14: C57.1, JP15.3, U15.5
X15: C61.1, JP16.3, U16.5
X16: C65.1, JP17.3, U17.5
X17: C69.1, JP18.3, U18.5
X18: C73.1, JP19.3, U19.5
X19: C77.1, JP20.3, U20.5
X20: C81.1, JP21.3, U21.5
X21: C85.1, JP22.3, U22.5
X22: C89.1, JP23.3, U23.5
X23: C93.1, JP24.3, U24.5
X24: C97.1, JP25.3, U25.5
X25: C101.1, JP26.3, U26.5
X26: C105.1, JP27.3, U27.5
X27: C109.1, JP28.3, U28.5
X28: C113.1, JP29.3, U29.5
X29: C117.1, JP30.3, U30.5
X30: C121.1, JP31.3, U31.5
X31: C125.1, JP32.3, U32.5
X32: C129.1, JP33.3, U33.5
X33: C133.1, JP34.3, U34.5
X34: C137.1, JP35.3, U35.5
X35: C141.1, JP36.3, U36.5
Y: C2.1, JP1.4, U1.4
Y1: C6.1, JP2.4, U2.4
Y2: C10.1, JP3.4, U3.4
Y3: C14.1, JP4.4, U4.4
Y4: C18.1, JP5.4, U5.4
Y5: C22.1, JP6.4, U6.4
Y6: C26.1, JP7.4, U7.4
Y7: C30.1, JP8.4, U8.4
Y8: C34.1, JP9.4, U9.4
Y9: C38.1, JP10.4, U10.4
Y10: C42.1, JP11.4, U11.4
Y11: C46.1, JP12.4, U12.4
Y12: C50.1, JP13.4, U13.4
Y13: C54.1, JP14.4, U14.4
Y14: C58.1, JP15.4, U15.4
Y15: C62.1, JP16.4, U16.4
Y16: C66.1, JP17.4, U17.4
Y17: C70.1, JP18.4, U18.4
Y18: C74.1, JP19.4, U19.4
Y19: C78.1, JP20.4, U20.4
Y20: C82.1, JP21.4, U21.4
Y21: C86.1, JP22.4, U22.4
Y22: C90.1, JP23.4, U23.4
Y23: C94.1, JP24.4, U24.4
Y24: C98.1, JP25.4, U25.4
Y25: C102.1, JP26.4, U26.4
Y26: C106.1, JP27.4, U27.4
Y27: C110.1, JP28.4, U28.4
Y28: C114.1, JP29.4, U29.4
Y29: C118.1, JP30.4, U30.4
Y30: C122.1, JP31.4, U31.4
Y31: C126.1, JP32.4, U32.4
Y32: C130.1, JP33.4, U33.4
Y33: C134.1, JP34.4, U34.4
Y34: C138.1, JP35.4, U35.4
Y35: C142.1, JP36.4, U36.4
Z: C3.1, JP1.5, U1.16
Z1: C7.1, JP2.5, U2.16
Z2: C11.1, JP3.5, U3.16
Z3: C15.1, JP4.5, U4.16
Z4: C19.1, JP5.5, U5.16
Z5: C23.1, JP6.5, U6.16
Z6: C27.1, JP7.5, U7.16
Z7: C31.1, JP8.5, U8.16
Z8: C35.1, JP9.5, U9.16
Z9: C39.1, JP10.5, U10.16
Z10: C43.1, JP11.5, U11.16
Z11: C47.1, JP12.5, U12.16
Z12: C51.1, JP13.5, U13.16
Z13: C55.1, JP14.5, U14.16
Z14: C59.1, JP15.5, U15.16
Z15: C63.1, JP16.5, U16.16
Z16: C67.1, JP17.5, U17.16
Z17: C71.1, JP18.5, U18.16
Z18: C75.1, JP19.5, U19.16
Z19: C79.1, JP20.5, U20.16
Z20: C83.1, JP21.5, U21.16
Z21: C87.1, JP22.5, U22.16
Z22: C91.1, JP23.5, U23.16
Z23: C95.1, JP24.5, U24.16
Z24: C99.1, JP25.5, U25.16
Z25: C103.1, JP26.5, U26.16
Z26: C107.1, JP27.5, U27.16
Z27: C111.1, JP28.5, U28.16
Z28: C115.1, JP29.5, U29.16
Z29: C119.1, JP30.5, U30.16
Z30: C123.1, JP31.5, U31.16
Z31: C127.1, JP32.5, U32.16
Z32: C131.1, JP33.5, U33.16
Z33: C135.1, JP34.5, U34.16
Z34: C139.1, JP35.5, U35.16
Z35: C143.1, JP36.5, U36.16

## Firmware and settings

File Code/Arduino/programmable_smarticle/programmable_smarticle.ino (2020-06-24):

#include <Smarticle.h>


Smarticle smart(1);

void setup() {
  randomSeed(analogRead(A7));
  NeoSerial1.attachInterrupt(handleRxChar);
  smart.init_t4();
  smart.toggle_led(1);
  delay(3000);
  smart.toggle_led(0);
}

void loop() {
  smart.read_sensors();
  smart.transmit_data();
  smart.manage_msg();
}


ISR(TIMER4_COMPA_vect){
  smart.t4_interrupt();
}

static void handleRxChar( uint8_t c)
{
  smart.rx_interrupt(c);
}

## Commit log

2019-08-30 added arduino Libraries
2019-08-30 stream servo cpp work
2019-09-10 stream servo work
2019-09-11 change init mode
    This commit changes init_mode() so that only changing to IDLE resests all flags (_transmit, _read_sensors, _run_servos, etc.) Before this happened whenever a mode change occurred. However, for upcoming experiments where we will be switching between stream and gait interpolate.
    Additionally, this commit changes init_mode so that _gaitL and _gaitR are not reset to default values when switching into the INTERP mode, only when switching into the IDLE mode.
2019-09-11 Update Smarticle.cpp
    Deleted blocking while statement in rx_interrupt. Not sure how this will work as the interrupt tries to read something main() is writing to
2019-09-12 rename to StreamThread and change implementation to be subclass of Thread
2019-09-13 Update StreamThread
    changed thread_flag to run_flag
    changed broadcast to command
    fixed bytearray bug
2019-09-13 stream work
    things are kinda broken now; deleted _run_servos flag and just have enable/disable interrupts. We'll see if this is a good idea lol
2019-09-16 stream servo example
    change rx callback to not decode messages
2019-09-18 random stream delay
    option to set delay after command is received so that smarticles getting streamed commands are not in sync. Also changed attach_servos() so that it will only execute when servos are detached.
2019-09-18 stream servo delay work
2019-11-01 v2 updates
    changed software serial to hardware serial
    updated pins for sensors and servos
2019-11-21 bug fixes + single pose streaming
    fixed bug of multiple devices printing. Added simple stream functionality with example
2019-11-23 fixed printing issues
    changed debug to default to zero and will automatically print discovery messages
2019-12-11 update sync thread
    changed sync period to match gait period and added sync time list
2020-01-20 change to random corners
    also fix bug so that angR is written to right servo
2020-02-03 add functionality for switching between gaits
2020-02-13 no syntax errors woot!!
    [programmable_smarticle.ino]
2020-06-19 work on new servo stream
2020-06-24 add hardware files
    [192mm_ring.SLDPRT, 192mm_ring.STL, 200mm_ring_thirds.SLDPRT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]
2020-10-21 pcbway params

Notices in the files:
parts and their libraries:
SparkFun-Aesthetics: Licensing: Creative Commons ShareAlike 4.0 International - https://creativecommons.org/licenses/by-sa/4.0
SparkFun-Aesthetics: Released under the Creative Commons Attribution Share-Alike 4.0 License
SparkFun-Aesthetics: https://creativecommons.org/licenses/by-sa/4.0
